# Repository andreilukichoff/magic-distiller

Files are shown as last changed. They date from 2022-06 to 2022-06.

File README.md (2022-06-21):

The purpose of this project is to automate simple rectification equipment.

Hardware part is based on Espressif ESP32 MCU and software part is based on ESP-IDF framework and FreeRTOS, implementing asynchronous event-driven architecture.

# Prerequisites

It is assumed that the ESP-IDF 4.4.1 framework is installed at the default path (`~/esp/esp-idf`) and <a href="https://github.com/UncleRus/esp-idf-lib">esp-idf-lib</a> is installed at `~/esp/esp-idf-lib`. <a href="https://docs.espressif.com/projects/esp-idf/en/stable/esp32/get-started/index.html#installation-step-by-step">Follow this guide to install ESP-IDF.</a>

## Equipment

This project was developed and tested on a rectification column made of glass with a diameter of 50mm, a length of 1500mm, filled with a 3.5x3.5mm spiral prismatic packing, with a temperature sensor installed at a distance of 500mm from the bottom. Column set up on top of 25L steel tank with 2kW induction plate.

## Electronic components

* 1x Espressif ESP32 DevKitC board (`esp32-wroom-32d`/`esp32-wroom-32u`)
* 1x DS18B20 temperature sensor in metal sleeve with wiring
* 1x SH1106 or compatible I2C display
* 1x 5.1kΩ pull-up resistor
* 1x 12V 2-channel **[NO]** relay module
* 2x 12V **[NC]** water valves
* 1x 12V DC power supply (for valves and relays)
* 1x 12V/5V DC/DC converter module **OR** Micro-USB power supply (for MCU, display and sensors)
* 6x **[NO]** push buttons
* 1x Passive buzzer (not required but useful)

Some ESP32 boards have flashing issues (flashing won't start or stucks at random time), in that case you should mount the following additional components:

* 1x 10kΩ pull-up resistor (R2)
* 1x 10µF capacitor (C1)

With this mod you will be able to flash MCU flawlessly and without pressing the FLASH button.

# Schematic

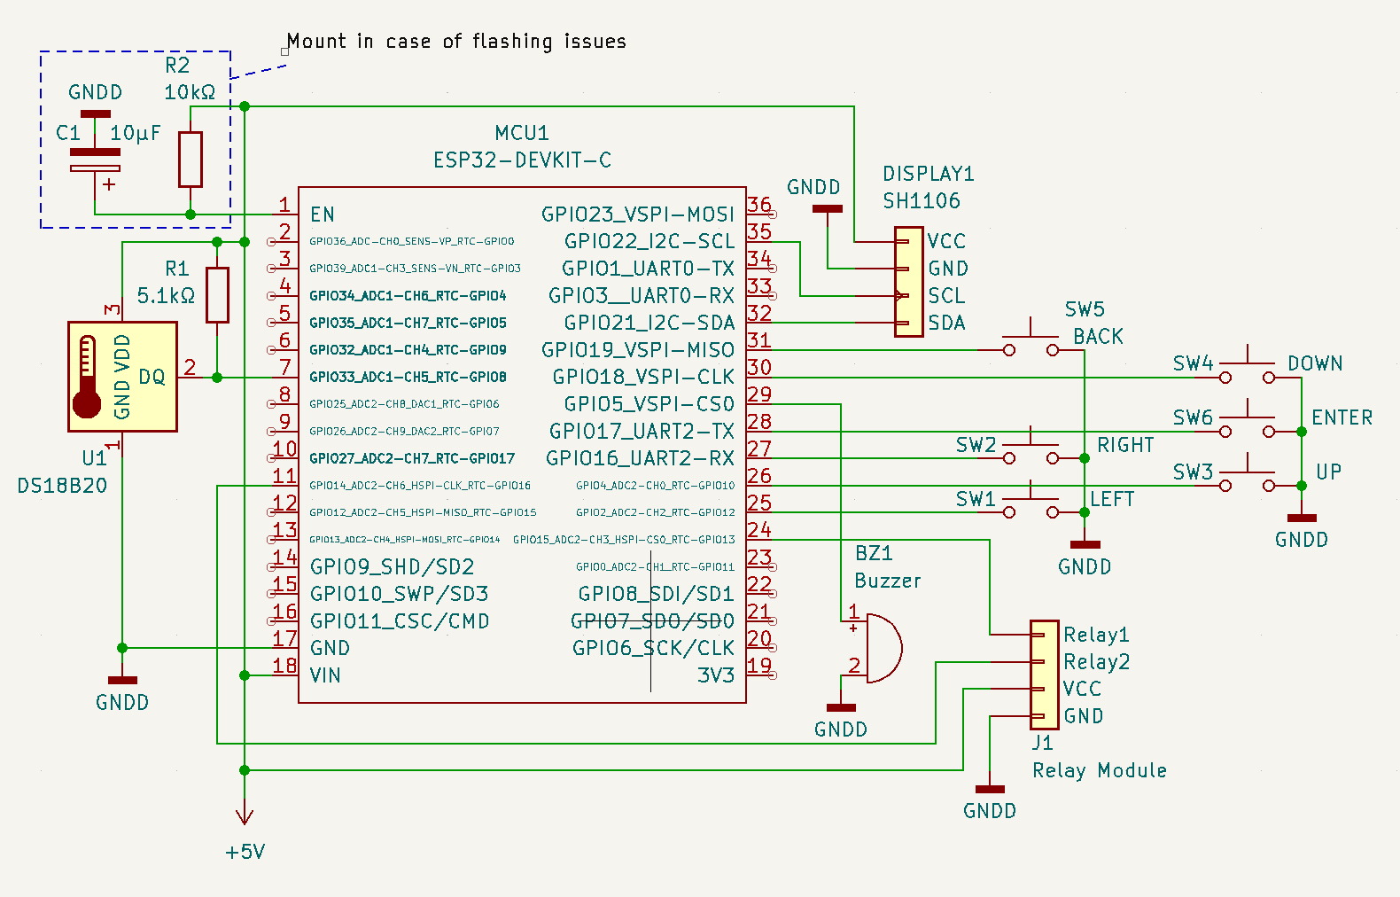
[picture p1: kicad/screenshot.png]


# Operating principle

The control program is in fact a finite state machine. Each state corresponds to the real physical state of the equipment.

1. **Warming up and initial stabilization.** The liquid is heated up to the boiling point which is detected by the rising and then constant temperature for a given time. Then the transition to the stabilization state is applied.
2. **Initial stabilization.** Constant temperature monitoring is applied.  When the temperature became constant and does not exceed the limit within the set time, stabilization is considered successful and collection of the ether-aldehyde fraction begins. Otherwise the process stops and message "Unable to stabilize" displayed.
3. **Collection of the ether-aldehyde fraction (heads).** The first valve (calibrated for a lower throughput) opens and filling of the first container begins. In the current version operator should watch when the ether-aldehyde fraction ends and transit to the next state manually using the control button.
4. **Collection of the body (hearts).** The ether-aldehyde fraction valve closes, and the main valve (calibrated for a higher throughput) opens and the filling of the second container begins. During the collection process, the temperature is monitored. If the temperature exceeds the threshold, a transition to the stabilization state is applied (see below). If stabilization succeeds, the transition to the collection of the body is applied. If stabilization fails, the entire process is considered complete.
5. **Stabilization.** This state is entered from collection of the body if temperature conditions are not met. When the temperature became constant and does not exceed the limit within the set time, stabilization is considered successful and collection of the body resumes, otherwise (or if the temperature rises fast) the transition to "completed" state is applied.
6. **Collection completed.** Both valves are closed. This is the final state and no transition to any state is allowed (unless manually triggered by button).

### TO DO:

* Automate collection of ether-aldehyde fraction
* Implement barometric compensation
* Implement heating element power switching
* Implement cooling water supply valve switching / cooling pump and fan switching
* Implement emergency monitoring (overheating, overflow, water leak, ethanol vapor, smoke, etc.)
* Implement remote control over Wi-Fi/Bluetooth connection

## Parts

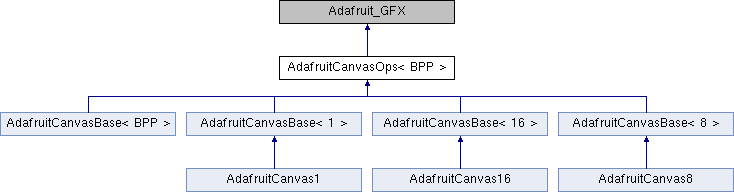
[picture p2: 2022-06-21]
components/ssd1306/docs/class_adafruit_canvas_ops.png

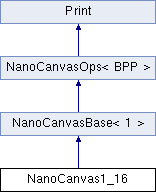
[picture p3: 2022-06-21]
components/ssd1306/docs/class_nano_canvas1__16.png

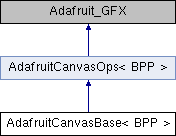
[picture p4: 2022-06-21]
components/ssd1306/docs/class_adafruit_canvas_base.png

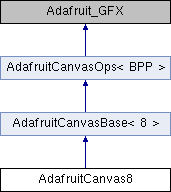
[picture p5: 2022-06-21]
components/ssd1306/docs/class_adafruit_canvas8.png

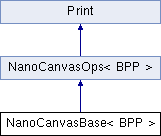
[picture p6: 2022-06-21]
components/ssd1306/docs/class_nano_canvas_base.png

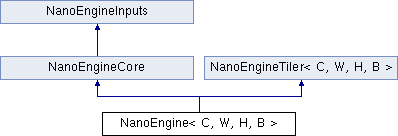
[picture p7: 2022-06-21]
components/ssd1306/docs/class_nano_engine.png

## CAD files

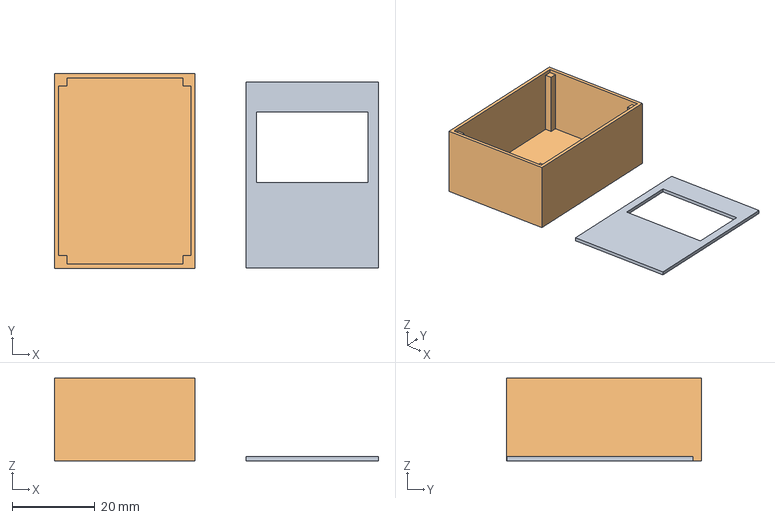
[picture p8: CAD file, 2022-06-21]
components/ssd1306/examples/games/arkanoid/schematics/case.3mf
78.3 x 47.0 x 20.0 mm

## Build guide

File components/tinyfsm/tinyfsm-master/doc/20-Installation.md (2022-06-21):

Installation
============

TinyFSM is an header-only library, no special installation steps are
needed. Just point your compiler to the "include" directory, and in
your source files:

    #include <tinyfsm.hpp>

Prerequisites
-------------

TinyFSM requires a compiler supporting the C++11 language standard
("-std=c++11" in gcc).

TinyFSM does not depend on RTTI, exceptions or any external library.
If you need to compile without standard libraries (e.g. in conjunction
with `-nostdlib` linker option), add `-DTINYFSM_NOSTDLIB` to the
compiler options: this removes all dependencies on the standard
library by disabling some compile-time type checks.

Building the Elevator Example
-----------------------------

Change to the elevator example directory and compile the sources:

    $ cd examples/elevator
    $ make

Our elevator has call buttons on every floor, sensors reporting the
current position, and an alarm button for emergency. These actors can
be triggered via a simple command interface:

    $ ./elevator
    Motor: stopped
    Motor: stopped
    c=Call, f=FloorSensor, a=Alarm, q=Quit ?

Let's call the elevator to floor 2:

    c=Call, f=FloorSensor, a=Alarm, q=Quit ? c
    Floor ? 2
    Motor: moving up
    c=Call, f=FloorSensor, a=Alarm, q=Quit ?

Now the elevator is moving up, and we need to trigger the floor sensor:

    c=Call, f=FloorSensor, a=Alarm, q=Quit ? f
    Floor ? 1
    Reached floor 1
    c=Call, f=FloorSensor, a=Alarm, q=Quit ? f
    Floor ? 2
    Reached floor 2
    Motor: stopped
    c=Call, f=FloorSensor, a=Alarm, q=Quit ?

Now we simulate a sensor defect:

    c=Call, f=FloorSensor, a=Alarm, q=Quit ? c
    Floor ? 1
    Motor: moving down
    c=Call, f=FloorSensor, a=Alarm, q=Quit ? f
    Floor ? 2
    Floor sensor defect (expected 1, got 2)
    *** calling maintenance ***
    Motor: stopped

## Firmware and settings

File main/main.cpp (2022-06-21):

/*
 * The MIT License
 *
 * Copyright (c) 2022 Andrei Lukichev
 *
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
 * THE SOFTWARE IS PROVIDED "AS IS", WITHOUT WARRANTY OF ANY KIND, EXPRESS OR
 * IMPLIED, INCLUDING BUT NOT LIMITED TO THE WARRANTIES OF MERCHANTABILITY,
 * FITNESS FOR A PARTICULAR PURPOSE AND NONINFRINGEMENT. IN NO EVENT SHALL THE
 * AUTHORS OR COPYRIGHT HOLDERS BE LIABLE FOR ANY CLAIM, DAMAGES OR OTHER
 * LIABILITY, WHETHER IN AN ACTION OF CONTRACT, TORT OR OTHERWISE, ARISING FROM,
 * OUT OF OR IN CONNECTION WITH THE SOFTWARE OR THE USE OR OTHER DEALINGS IN
 * THE SOFTWARE.
 */

#include <freertos/FreeRTOS.h>
#include <freertos/task.h>
#include <esp_log.h>
#include <esp_err.h>
#include <i2cdev.h>
#include <ds18x20.h>
#include <cstring>
#include <nvs_flash.h>
#include <freertos/timers.h>

#include "sdkconfig.h"
#include "common.h"
#include "hw/TimeHelper.h"
#include "tinyfsm.hpp"
#include "states/Distiller.h"
#include "events/DistillerEvent.h"
#include "button.h"
#include "Buzzer.h"
#include "ssd1306.h"
#include "buttons.h"
#include "states/Greeting.h"

static const char *TAG = "main";

FSM_INITIAL_STATE(Distiller, Greeting)

void dispatch_queue_event() {
    DistillerEvent *event_p = nullptr;
    if ((pdTRUE == xQueueReceive(Distiller::eventQueue, &event_p, pdMS_TO_TICKS(100)) && (event_p != nullptr))) {
        //ESP_LOGI(TAG, "dispatch event, type: %d", (int) event_p->_type);

        switch (event_p->_type) {
            case DistillerEventType::ButtonClick: {
                ESP_LOGI(TAG, "Received ButtonClick");
                auto event = reinterpret_cast<ButtonClickDistillerEvent *>(event_p);
                Distiller::dispatch(*event);
                break;
            }
            case DistillerEventType::TimerTick: {
                //sESP_LOGI(TAG, "Received TimerTick");
                auto event = reinterpret_cast<TimerTickEvent *>(event_p);
                Distiller::dispatch(*event);
                break;
            }
            case DistillerEventType::InitialStabilizationDone: {
                ESP_LOGI(TAG, "Received InitialStabilizationDone");
                auto event = reinterpret_cast<InitialStabilizationDoneEvent *>(event_p);
                Distiller::dispatch(*event);
                break;
            }
            case DistillerEventType::InitialStabilizationImpossible: {
                ESP_LOGI(TAG, "Received InitialStabilizationImpossible");
                auto event = reinterpret_cast<InitialStabilizationImpossibleEvent *>(event_p);
                Distiller::dispatch(*event);
                break;
            }
            case DistillerEventType::HeadsDistillingDone: {
                ESP_LOGI(TAG, "Received HeadsDistillingDone");
                auto event = reinterpret_cast<HeadsDistillingDoneEvent *>(event_p);
                Distiller::dispatch(*event);
                break;
            }
            case DistillerEventType::HeartsDistillingDone: {
                ESP_LOGI(TAG, "Received HeartsDistillingDone");
                auto event = reinterpret_cast<HeartsDistillingDoneEvent *>(event_p);
                Distiller::dispatch(*event);
                break;
            }
            case DistillerEventType::HeartsDistillingTempExceeded: {
                ESP_LOGI(TAG, "Received HeartsDistillingTempExceeded");
                auto event = reinterpret_cast<HeartsDistillingTempExceededEvent *>(event_p);
                Distiller::dispatch(*event);
                break;
            }
            case DistillerEventType::HeartsDistillingTempStabilized: {
                ESP_LOGI(TAG, "Received HeartsDistillingTempStabilized");
                auto event = reinterpret_cast<HeartsDistillingTempStabilizedEvent *>(event_p);
                Distiller::dispatch(*event);
                break;
            }
            case DistillerEventType::HeartsDistillingUnableToStabilizeTemp: {
                ESP_LOGI(TAG, "Received HeartsDistillingUnableToStabilizeTemp");
                auto event = reinterpret_cast<HeartsDistillingUnableToStabilizeTempEvent *>(event_p);
                Distiller::dispatch(*event);
                break;
            }
//            case DistillerEventType::TurnOff: {
//                auto event = reinterpret_cast<TurnOff *>(event_p);
//                Distiller::dispatch(*event);
//            }
//                break;

            default:
                break;
        }
        delete (event_p);
    }
}

[[noreturn]] void sensor_column_task(void *) {
    ESP_LOGI(TAG, "starting column sensor update task\n");
    for (;;) {
        Distiller::columnSensor.update();
    }
    vTaskDelete(NULL);
}

[[noreturn]] void sensor_def_task(void *) {
    ESP_LOGI(TAG, "starting def sensor update task\n");
    for (;;) {
        Distiller::defSensor.update();
    }
    vTaskDelete(NULL);
}

[[noreturn]] void sensor_tank_task(void *) {
    ESP_LOGI(TAG, "starting tank sensor update task\n");
    for (;;) {
        Distiller::tankSensor.update();
    }
    vTaskDelete(NULL);
}

[[noreturn]] void dispatch_task(void *) {
    ESP_LOGI(TAG, "starting dispatch_task\n");
    for (;;) {
        dispatch_queue_event();
    }
    vTaskDelete(NULL);
}

extern "C" void app_main() {
    ESP_LOGI(TAG, "initializing hardware");
    sh1106_128x64_i2c_init();
    ssd1306_setFixedFont(ssd1306xled_font6x8);
    ssd1306_clearScreen();

    init_buttons();
    Distiller::buzzer.init(BUZZER_GPIO);

    ESP_LOGI(TAG, "initializing distiller state machine");

    Distiller::start();

    ESP_LOGI(TAG, "creating tasks");

    xTaskCreate(dispatch_task, "dispatch_task", configMINIMAL_STACK_SIZE * 20, nullptr, 5, nullptr);
    xTaskCreate(sensor_def_task, "sensor_def_task", configMINIMAL_STACK_SIZE * 5, nullptr, 5, nullptr);
    xTaskCreate(sensor_column_task, "sensor_column_task", configMINIMAL_STACK_SIZE * 5, nullptr, 5, nullptr);
    xTaskCreate(sensor_tank_task, "sensor_tank_task", configMINIMAL_STACK_SIZE * 5, nullptr, 5, nullptr);
}

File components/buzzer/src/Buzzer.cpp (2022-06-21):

#include <driver/ledc.h>
#include <freertos/FreeRTOS.h>
#include <freertos/task.h>
#include "Buzzer.h"

void Buzzer::init(gpio_num_t gpio) {
    gpio_ = gpio;

    gpio_config_t io_conf;
    io_conf.intr_type = GPIO_INTR_DISABLE;
    io_conf.mode = GPIO_MODE_OUTPUT;
    io_conf.pin_bit_mask = (1ULL << gpio_);
    io_conf.pull_down_en = GPIO_PULLDOWN_DISABLE;
    io_conf.pull_up_en = GPIO_PULLUP_DISABLE;
    gpio_config(&io_conf);
    gpio_set_level(gpio_, 0);
}

void Buzzer::beep(piano_note_t key_num, uint16_t dur_hms) {
    periph_module_enable(PERIPH_LEDC_MODULE);
    ledc_timer_config_t ledc_timer;
    ledc_channel_config_t ledc_channel;

    ledc_timer.freq_hz = notes[key_num];                        // frequency of PWM signal
    ledc_timer.duty_resolution = LEDC_TIMER_13_BIT;    // resolution of PWM duty
    ledc_timer.speed_mode = LEDC_LOW_SPEED_MODE;            // timer mode
    ledc_timer.timer_num = LEDC_TIMER_0;            // timer index
    ledc_timer.clk_cfg = LEDC_AUTO_CLK;

    // Set configuration of timer0 for high speed channels

    ledc_channel.channel = LEDC_CHANNEL_0;
    ledc_channel.duty = 4095;
    ledc_channel.gpio_num = gpio_;
    ledc_channel.speed_mode = LEDC_LOW_SPEED_MODE;
    ledc_channel.hpoint = 0;
    ledc_channel.timer_sel = LEDC_TIMER_0;
    ledc_channel.intr_type = LEDC_INTR_DISABLE;

    ledc_timer_config(&ledc_timer);
    ledc_channel_config(&ledc_channel);

    vTaskDelay(pdMS_TO_TICKS(dur_hms));
    ledc_stop(LEDC_LOW_SPEED_MODE, LEDC_CHANNEL_0, 0);
}

void Buzzer::beep_btn() {
    beep(NOTE_B5, 25);
}

void Buzzer::beep_bad() {
    beep(NOTE_B3, 25);
    vTaskDelay(pdMS_TO_TICKS(10));
    beep(NOTE_B3, 25);
    vTaskDelay(pdMS_TO_TICKS(10));
    beep(NOTE_B3, 25);
}

void Buzzer::beep_toobad() {
    for (int i = 0; i < 3; ++i) {
        beep(NOTE_B6, 1000);
        beep(NOTE_B4, 1000);
    }
}

void Buzzer::beep_attention() {
    for (int n = 0; n < 3; ++n) {
        for (int i = 0; i < 3; ++i) {
            for (int j = 0; j < 3; ++j) {
                beep(NOTE_B5, 50);
                vTaskDelay(pdMS_TO_TICKS(10));
                beep(NOTE_B6, 50);
                vTaskDelay(pdMS_TO_TICKS(20));
            }
            vTaskDelay(pdMS_TO_TICKS(250));
        }
        vTaskDelay(pdMS_TO_TICKS(250));
    }
}

void Buzzer::beep_good() {
    for (int i = 0; i < 1; ++i) {
        beep(NOTE_B4, 125);
        vTaskDelay(pdMS_TO_TICKS(50));
        beep(NOTE_C5, 125);
        vTaskDelay(pdMS_TO_TICKS(50));
        beep(NOTE_D5, 125);
        vTaskDelay(pdMS_TO_TICKS(50));
        beep(NOTE_E5, 125);
        vTaskDelay(pdMS_TO_TICKS(50));
        beep(NOTE_F5, 125);
        vTaskDelay(pdMS_TO_TICKS(50));
        beep(NOTE_G5, 125);
        vTaskDelay(pdMS_TO_TICKS(50));
        beep(NOTE_A5, 125);
        vTaskDelay(pdMS_TO_TICKS(50));
    }
}
